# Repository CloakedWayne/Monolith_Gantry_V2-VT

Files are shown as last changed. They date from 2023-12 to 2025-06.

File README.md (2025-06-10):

[][cc-by-nc-sa]

# Monolith Gantry R1
> [!IMPORTANT]
> **There is no step-by-step build guide or detailed documentation yet.**
> 
> **The sheet metal version is more difficult to build than what the average Voron user is used to. Please evaluate the required patience and skill levels before proceeding.**

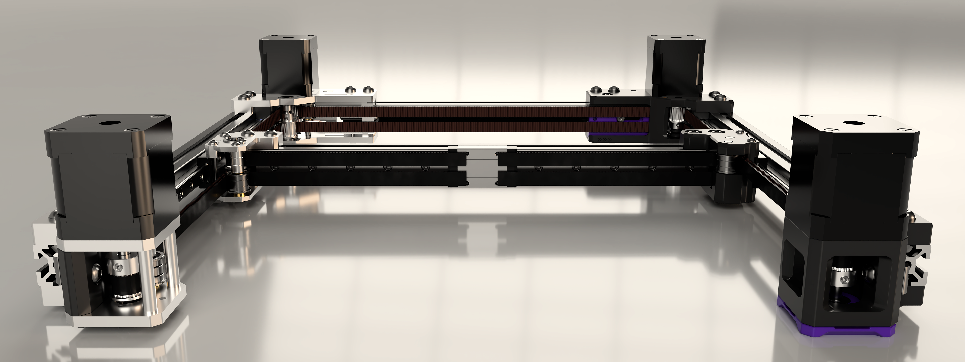
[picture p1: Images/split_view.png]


## What's this?
This is a performance-oriented, configurable gantry platform for Voron 2.4 and Trident.

### Drive configurations:
- 2WD
- AWD

### Belt widths:
- 6mm
- 9mm

 ### Materials:
- Printed
- Sheet metal

## What's new with Monolith R1?
- Updated styling
- More shared parts between 6 and 9mm
- Sheet metal options
- Can fit into a stock 2020 frame at the cost of some Y-overtravel with the added no-protrusion mode
- Much better tensioner travel
- No toothed idlers

### [Configurator and BOM - Google Sheets ](https://docs.google.com/spreadsheets/d/14mWAb1CxOuovr1oKOu4pIA4AFW-SMeCLfFVxeun0VMA/edit?usp=sharing)

<br/>

> [!NOTE]
> **If you have questions or want to stay more up-to-date with Monolith, consider joining the dedicated Discord server.**
>
> Join the Discord (https://discord.gg/JanBKxAzDz)
>
> **If you would like to see more of this and other projects in the future, consider supporting me on Ko-fi.**
>
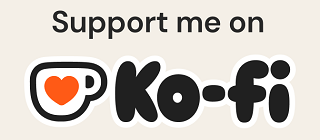
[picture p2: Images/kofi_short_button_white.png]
Join the Discord (https://ko-fi.com/cloakedwayne)
> 

## 2025 Roadmap
- Milled 9mm AWD kits
- Monolith CPAP SLM toolhead
- Better documentation

## Design goals
- The shortest and the simplest belt path possible with AWD compatibility
- The shortest moment arms possible for increased rigidity even when reusing hardware and motion parts
- Double shear steppers and live shaft idlers for higher belt tensions and better reliability
- Good-looking design
- Cheap BOM

## Performance expectations
**2WD:** Due to the 10-15cm shorter belt path, with stiffer and lighter XY-joints the printer should perform similarly to a 50mm smaller one equipped with the same X-axis setup.

**AWD:** It doesn't come at the cost of adding 20cm belt length and idlers, so input shaper scaling can be close to +100% compared to 2WD due to the truly halved effective belt length. But only when no toolhead or frame bottlenecks are limiting its scaling.

**9mm belts:** Wider belts can offer an additional 50% input shaper scaling on top of what's described above.

## What's the catch?
- you have to build a well-balanced system: the increased effective belt stiffness with higher-end gantry configurations will amplify toolhead and frame rigidity issues
- Some toolheads are not yet compatible because of the different belt path
- Z-chain relocation or Z-umbilical is needed on V2
- Trident rear vertical extrusion brackets have to be rotated by 180 degrees or swapped to regular 2020 brackets based on the gantry configuration

## Acknowledgement
I want to thank:

- **[Sy-Noon](https://synoon.portfoliobox.net/)** for the awesome logo and feedback on general aesthetics
- **ifp, iniqy, krankydonkey, MoneyShot, Nicket, tktktktk, Zakfarias, Scarecrow, The Adeo** for testing and good feedback
- **ZaMarin** for FAQ
- **Armchair Heavy Industries** for the exposure and the moderation help I got in their user-project space
- **VoronDesign** for making V2.4 and Trident and for starting me on this journey to improve my FDM design skills
- anyone who helped me along the way

<br/><br/><br/><br/>
This work is licensed under a
[Creative Commons Attribution-NonCommercial-ShareAlike 4.0 International License][cc-by-nc-sa].

[][cc-by-nc-sa]

[cc-by-nc-sa]: http://creativecommons.org/licenses/by-nc-sa/4.0/
[cc-by-nc-sa-image]: https://licensebuttons.net/l/by-nc-sa/4.0/88x31.png
[cc-by-nc-sa-shield]: https://img.shields.io/badge/License-CC%20BY--NC--SA%204.0-lightgrey.svg

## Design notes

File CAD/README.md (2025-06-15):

### The [Monolith Configurator](https://docs.google.com/spreadsheets/d/14mWAb1CxOuovr1oKOu4pIA4AFW-SMeCLfFVxeun0VMA/edit?usp=sharing) will give you the links to the files you need for your build!

## Changelog

### 15.06.2025

- 695 W5 bearing support
- minor visual changes
- S45R long-shafted steppers in CAD
- subassembly fixes

### 10.06.2025

- sheet metal tensioner wire delete
- gantry-mounted X-endstop option

### 28.01.2025

- fixed subassembly origins
- fixed some naming oopsies
- ditched the printed alignment helpers for the sheet metal version
- more corner reliefs on motor mount plates
- smaller assembly/BOM fixes

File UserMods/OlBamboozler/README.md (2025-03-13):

<h1 align="left">Monolith X Endstop extender for Xol-Carriage</h1>

###

<p align="left">The current Monolith Xol carriage X endstop does not reach the XY joints on Monolith R1. <br><br>This is what I came up with to extend the join so that the endstop switch could reach.<br><br>All you need is 2 m3 square nuts, the same used in the carriage mount.</p>

###

<div align="center">
  
</div>

###

<h2 align="left">Monolith Rear Z Chain</h2>

###

<p align="left">Just a simple rear extrusion mount to clean up the wires going to the Z chain, fits a couple of 4 pin microfit connectors and some extra wiggle room.</p>

###

<div align="center">
  
</div>

###

<p align="left">Thanks to hydrorubi for the original Z-chain files. Any issues feel free to ping me on discord</p>

###

[](https://discordapp.com/users/360564967382056961)

###

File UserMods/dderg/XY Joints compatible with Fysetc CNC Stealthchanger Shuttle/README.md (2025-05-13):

# XY Joints compatible with Fysetc Stealthchanger Shuttle belt spacing

This mod moves X beam 2mm back, allowing to clamp the belts
from the front of the shuttle.

Made for 9mm belts, both AWD and 2WD, and after testing both, there's no gains with AWD due to stealthchanger limitations. You can expect about 4000mm/s^2 accelerations on a 350mm build

I recommend mounting the joints upside down (heatsets on the top) for better clearance when docking

You will loose 2mm of Y travel at the front, so make sure to adjust your dock positions accordingly

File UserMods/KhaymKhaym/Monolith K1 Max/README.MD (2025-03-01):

**** K1 Max Monolith Gantry ****
________________________________

Mod was produced by KhaymKhaym and BootyCallJones 
Based off the Monolith Gantry by CloakedWayned

Assembly Instructions are inside of the CAD file. (reference it ya turd)

DXF for the panel is good to go, use 3mm thick A36 CRS from Send Cut Send or other vendor. 

DXF for the steel reinforcements on the gantry does need to have K factor edit to ensure the bend is proper depending on the material you choose. With 304 Stainless steel the K factor is .66

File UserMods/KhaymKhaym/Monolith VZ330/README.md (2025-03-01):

**** VZ330 Monolith Gantry ****
_______________________________

Mod was produced by KhaymKhaym and Kaifas
Based off the Monolith Gantry by CloakedWayned

Assembly Instructions are inside of the CAD file. (reference it ya turd)

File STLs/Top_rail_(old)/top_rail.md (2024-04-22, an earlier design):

Top rail requires mirrored parts in some cases.

**AB** = normal, **CD** = mirrored

### Top rail:
- Right front belt on top: **AB**
- Left front belt on top: **CD**

|Toolhead|Drive|Front mounts (2x)|Rear mounts (2x)|Tensioners (2x)|XY joints (L + R)|
|---|---|---|---|---|---|
|AB|2WD|CD|CD|CD|AB|
|AB|4WD|AB|AB|AB|AB|
|CD|2WD|AB|AB|AB|CD|
|CD|4WD|CD|CD|CD|CD|

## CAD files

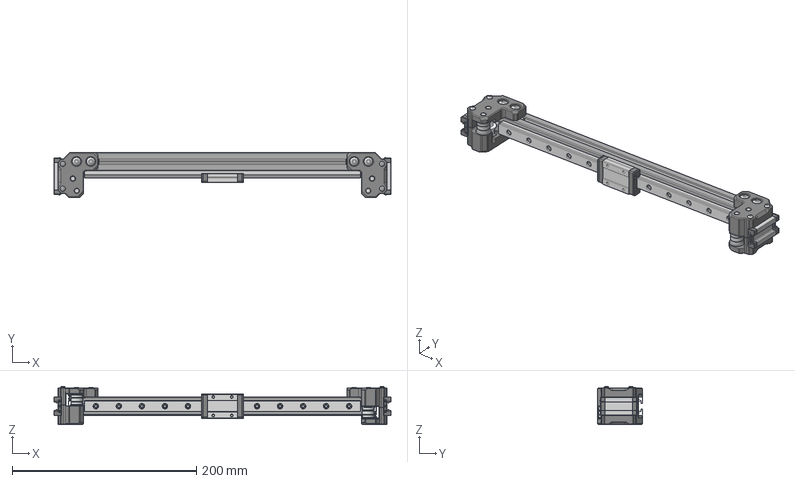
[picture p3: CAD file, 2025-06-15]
CAD/I_X_axes/_3_Printed_9mm_2WD_X_axis.step
366.0 x 49.2 x 41.8 mm
Printed_spacer x 4
F695 flanged bearing x 8
Shim 0.5mm x 10
M4x2.5 set screw x 4
GT2 20T 9mm pulley de-hubbed x 2
_MGN9H x 2
D5x40 smooth pin x 4
695 bearing x 2
Printed_9mm_2WD_XY_joint_right_a
Printed_9mm_2WD_XY_joint_right_b
M3x40 BHCS x 4
M3x6 BHCS x 8
M3xD5x4 threaded insert x 4
M5x12 BHCS x 6
Printed_9mm_2WD_XY_joint_left_a
Printed_9mm_2WD_XY_joint_left_b
M5 2020 drop-in T-nut x 6
_M3x8 SHCS x 12
_MGN12H

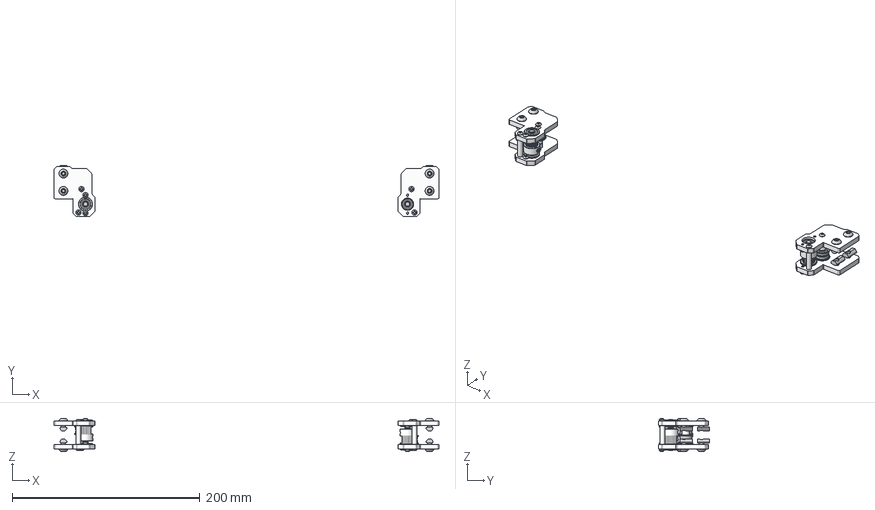
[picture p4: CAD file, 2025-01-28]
CAD/II_Front_motorless_mounts/_6_Sheet_metal_VT_6mm_front_motorless_mounts_FT.step
410.0 x 54.8 x 35.5 mm
Sheet_metal_VT_front_motorless_mount_a_4.7-5mm x 4
M3x6 BHCS x 8
M3xD5x20 threaded round standoff x 4
M3x8 BHCS x 8
M5x10 BHCS x 8
M5 2020 drop-in T-nut x 8
D5x30 smooth pin x 2
Shim 0.5mm x 4
Shim 1mm x 6
F695 flanged bearing x 8
GT2 20T 6mm pulley x 2
M5xD8x5 spacer x 4
Di=5mm L0=5mm compression spring x 2
Shim 0.2mm x 2

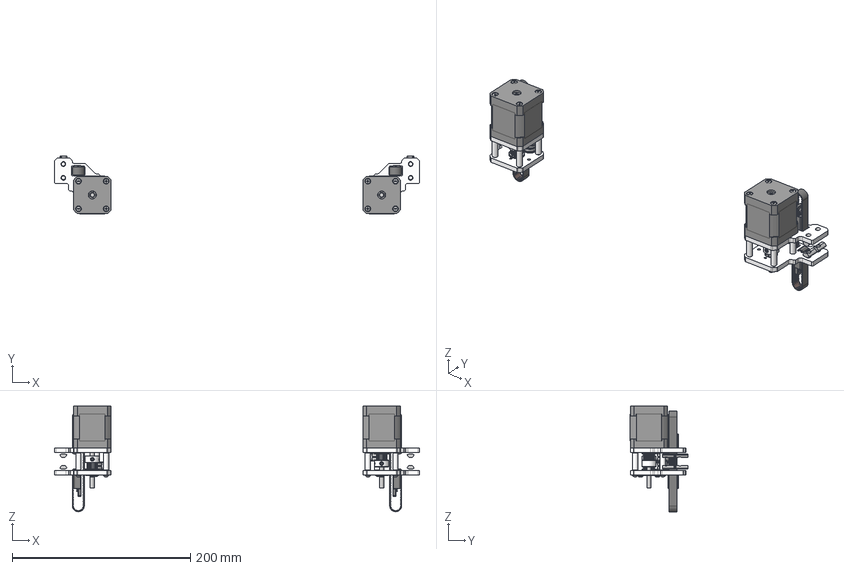
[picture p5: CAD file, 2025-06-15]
CAD/III_Front_motor_mounts/_17_Sheet_metal_V2_6mm_front_motor_mounts_FT_0.step
410.0 x 64.6 x 118.5 mm
Sheet_metal_V2_front_motor_mount_b_4.7-5mm x 2
M3xD6x20 spacer x 8
M3x35 BHCS x 8
M3 washer x 8
M3x6 BHCS x 4
M3x8 FHCS x 2
M3x8 BHCS x 2
M5 2020 drop-in T-nut x 8
M3xD5x20 threaded round standoff x 2
M5xD8x5 spacer x 4
F695 flanged bearing x 6
Shim 0.5mm x 4
Shim 1mm x 2
GT2 20T 6mm pulley x 2
_S45R shaft x 2
_stepper x 2
Sheet_metal_V2_front_motor_mount_a_4.7-5mm x 2
_Hybrid_SLM_V2_6mm_Z_belt x 2
Hybrid_SLM_V2_Z_belt_clip_a x 4
Hybrid_SLM_V2_Z_belt_clip_b x 4

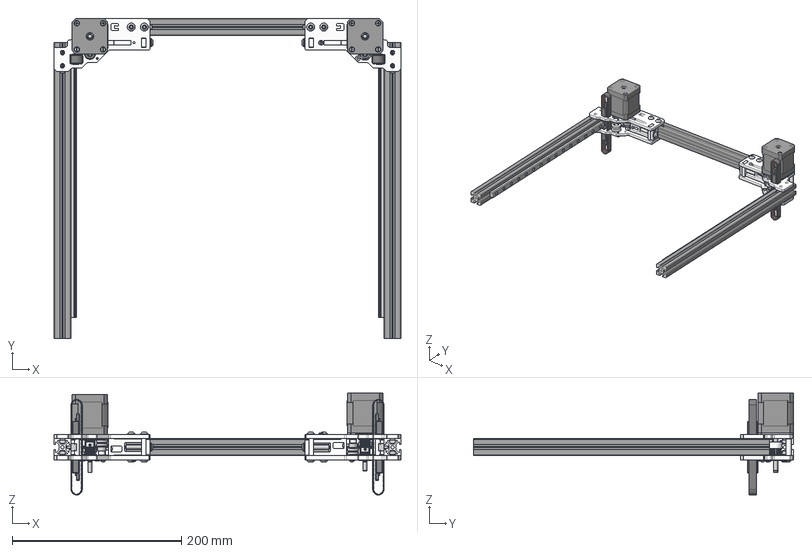
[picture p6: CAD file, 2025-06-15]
CAD/IV_Rear_motor_mounts/_20_Sheet_metal_V2_6mm_rear_motor_mounts_NP_0.step
410.0 x 378.1 x 120.5 mm
Sheet_metal_V2_rear_motor_mount_b_4.7-5mm x 2
Sheet_metal_6mm_tensioner_b_4.7-5mm x 2
Sheet_metal_V2_rear_motor_mount_a_4.7-5mm x 2
Sheet_metal_6mm_tensioner_a_4.7-5mm x 2
Sheet_metal_6mm_tensioner_c_4.7-5mm x 2
_Hybrid_SLM_V2_6mm_Z_belt x 2
Hybrid_SLM_V2_Z_belt_clip_a x 4
Hybrid_SLM_V2_Z_belt_clip_b x 4
M5 washer x 2
M3x6 FHCS x 8
M3x6 BHCS x 6
M5x30 BHCS x 2
M3 washer x 6
M3x35 BHCS x 6
M3xD6x20 spacer x 6
M5x10 BHCS x 8
M5 2020 drop-in T-nut x 16
M5xD10x5 shaft collar x 2
M5xD8x5 spacer x 2
M3x8 BHCS x 2
F695 flanged bearing x 10
GT2 20T 6mm pulley x 2
Shim 0.2mm x 2
Di=5mm L0=5mm compression spring x 2
D5x30 smooth pin x 4
Shim 1mm x 6
_S45R shaft x 2
_stepper x 2
GT2 20T 6mm pulley de-hubbed x 2
M4x2.5 set screw x 4
Shim 0.5mm x 2
Sheet_metal_6mm_spacer_a_2_or_2.5mm
_M3x8 SHCS x 30

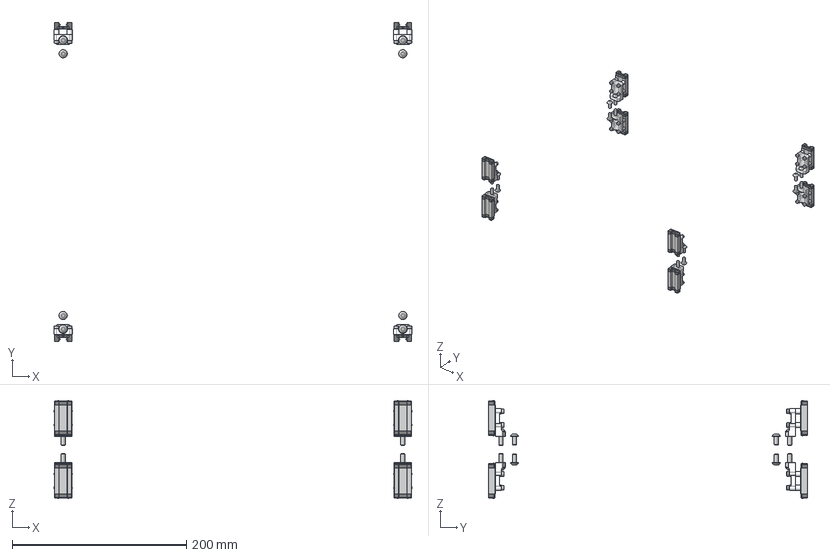
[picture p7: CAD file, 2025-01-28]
CAD/VI_V2_Z_joints/_37_SLM_V2_6mm_Z_joints_FT_NP_D.step
411.0 x 366.5 x 112.7 mm
_MGN9H x 8
SLM_V2_Z_joint x 8
M5x16 BHCS x 8
M3x10 SHCS x 16
M5x10 BHCS x 8
M3x16 SHCS x 16
M3xD6x6 spacer x 16

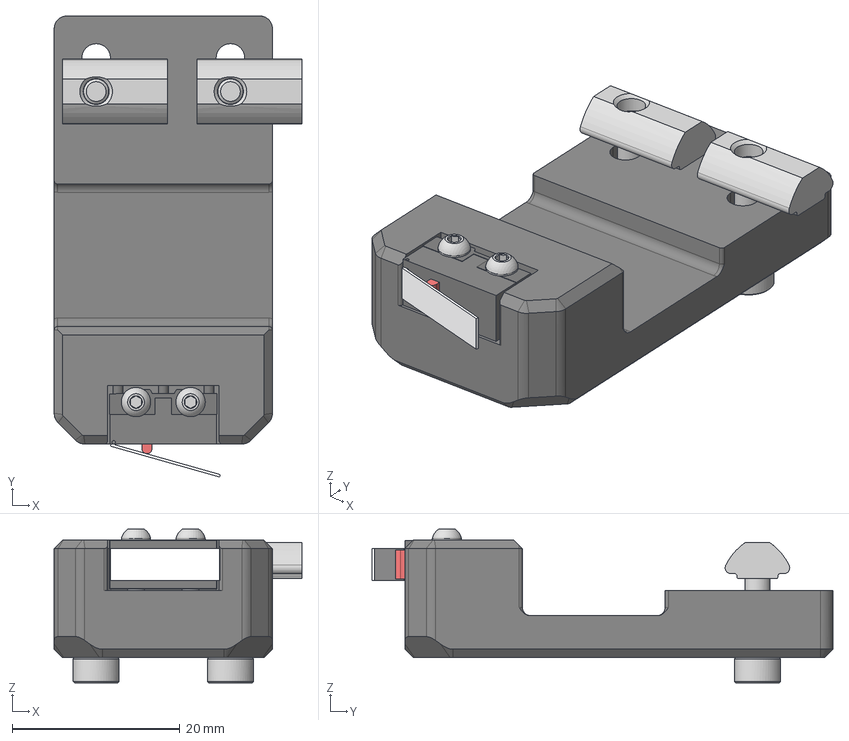
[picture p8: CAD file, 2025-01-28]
CAD/VII_Y_endstop/_2_V2_Y_endstop_NP.step
29.5 x 54.9 x 18.3 mm
KW10 microswitch
M2x10 self-tapping screw x 2
M3 2020 drop-in T-nut x 2
M3x12 SHCS x 2
Y_endstop_housing

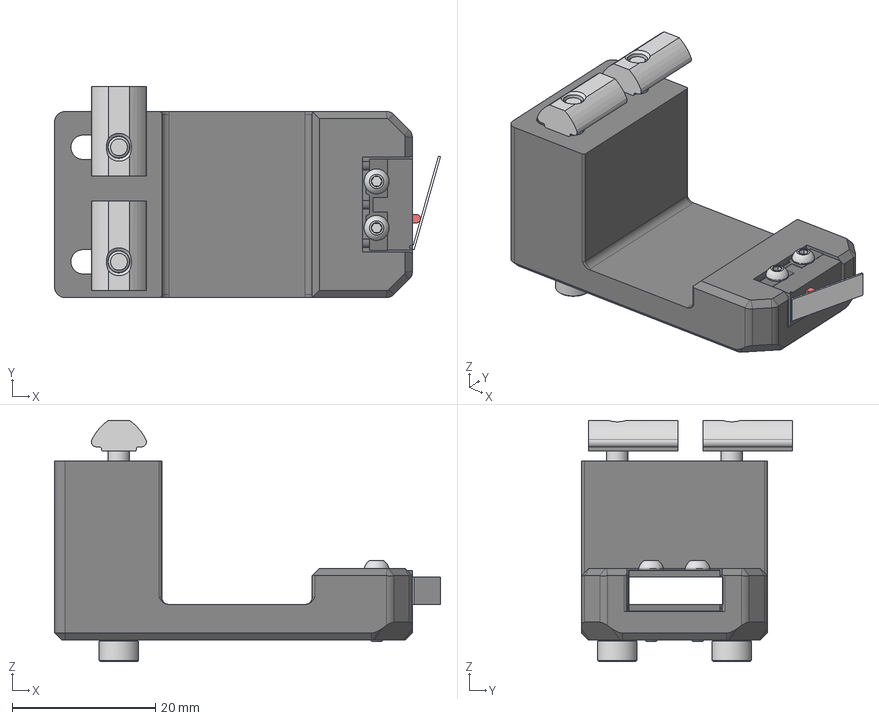
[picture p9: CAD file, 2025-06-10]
CAD/VIII_X_endstop/_1_X_endstop.step
53.9 x 29.5 x 33.7 mm
M3 2020 drop-in T-nut x 2
KW10 microswitch
M2x10 self-tapping screw x 2
M3x30 SHCS x 2
X_endstop_housing

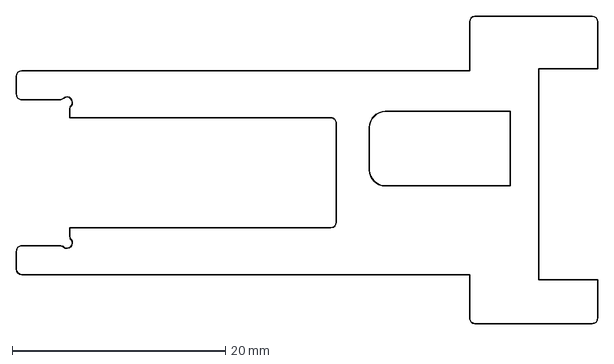
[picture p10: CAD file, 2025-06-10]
DXFs/Sheet_metal/Sheet_metal_6mm_specific/Sheet_metal_6mm_tensioner_a_4.7-5mm.dxf
54.5 x 28.8 mm

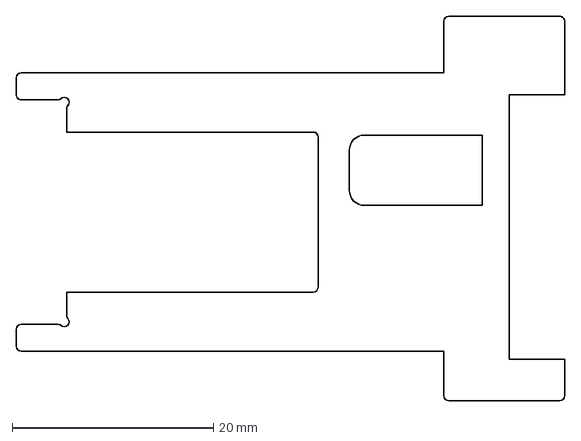
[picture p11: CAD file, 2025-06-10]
DXFs/Sheet_metal/Sheet_metal_9mm_specific/Sheet_metal_9mm_tensioner_a_4.7-5mm.dxf
54.5 x 38.2 mm

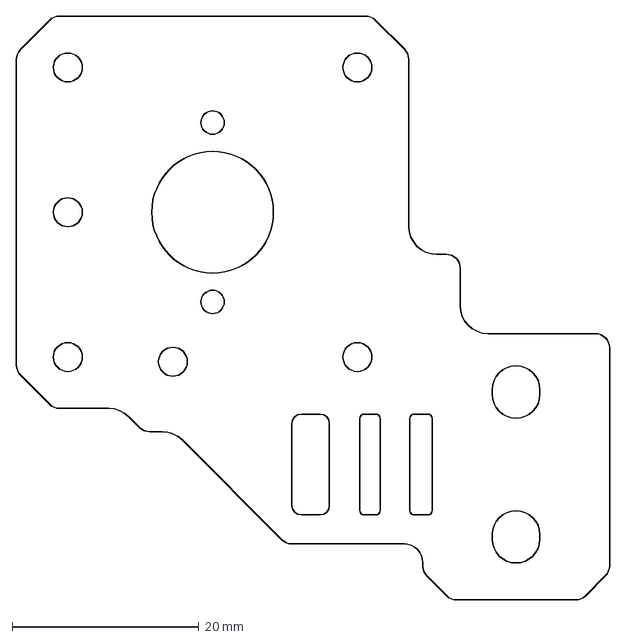
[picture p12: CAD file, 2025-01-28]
DXFs/Sheet_metal/Sheet_metal_V2_mounts/Sheet_metal_V2_front_motor_mount_b_4.7-5mm.dxf
63.5 x 62.5 mm

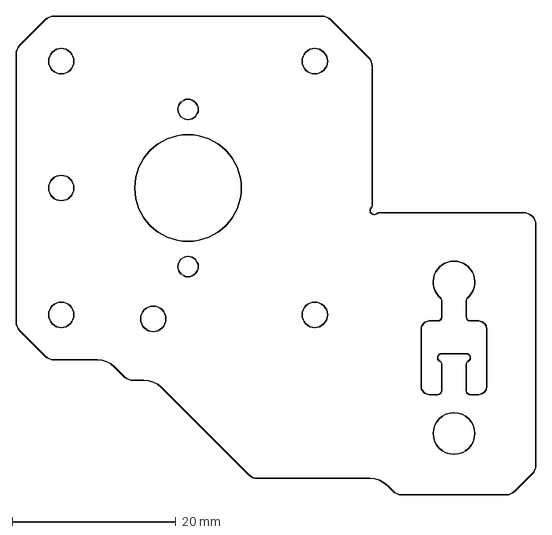
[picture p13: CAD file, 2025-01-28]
DXFs/Sheet_metal/Sheet_metal_VT_mounts/Sheet_metal_VT_front_motor_mount_b_4.7-5mm.dxf
63.5 x 58.5 mm

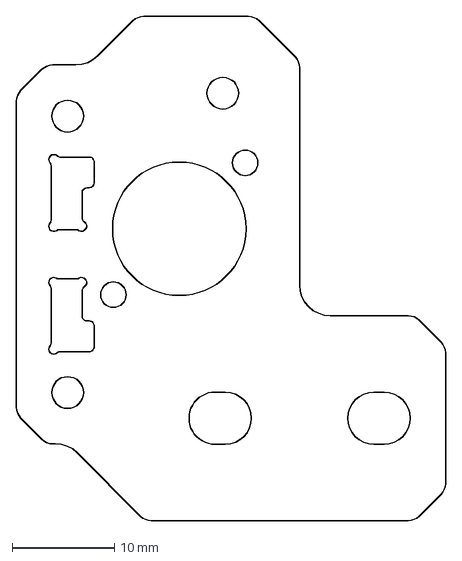
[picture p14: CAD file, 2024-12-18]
DXFs/Sheet_metal/Sheet_metal_XY_joints/Sheet_metal_XY_joint_a_3-3.2mm.dxf
41.9 x 49.2 mm

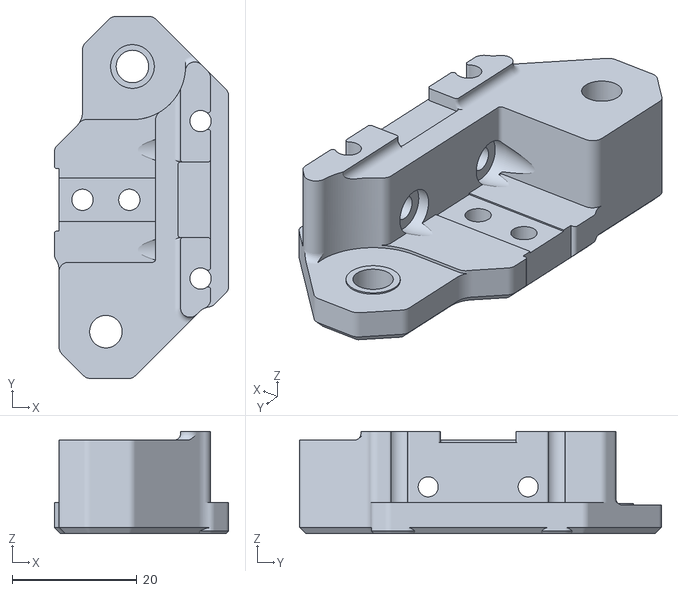
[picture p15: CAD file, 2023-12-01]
STLs/6mm_belts/Top_rail_6mm/AB/6mm_VZ-Hevort_XY_joints/6mm_VZ_Hevort_XY_joint_left_a.stl
27.9 x 57.9 x 16.4

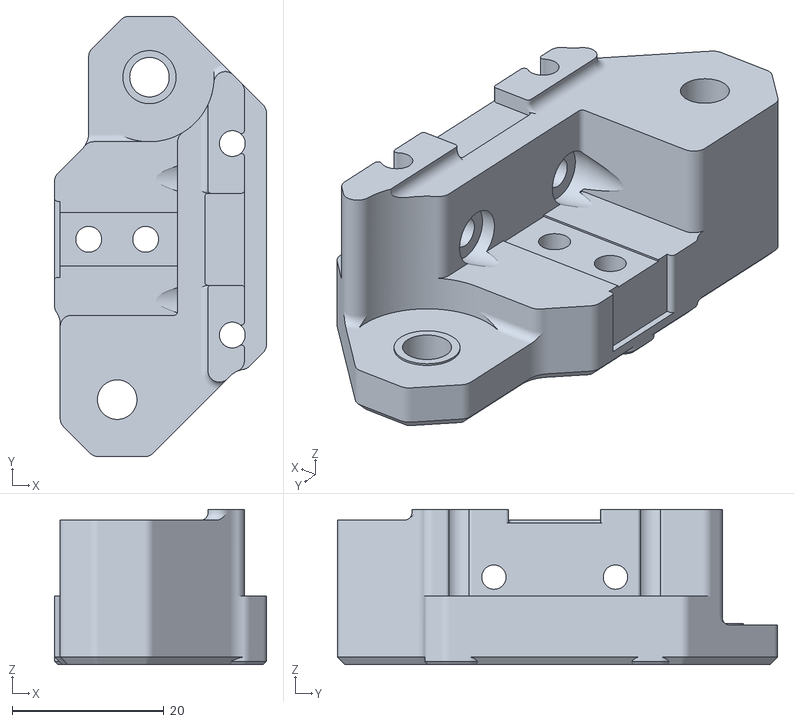
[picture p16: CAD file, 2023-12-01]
STLs/9mm_belts/Top_rail_9mm/AB/9mm_VZ-Hevort_XY_joints/9mm_VZ_Hevort_XY_joint_left_a.stl
27.9 x 57.9 x 20.4

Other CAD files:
STLs/Mounts/Printed_mounts/Printed_9mm_tensioner_b.stl
STLs/Mounts/Printed_mounts/Printed_V2_6mm_front_motor_mount/Printed_V2_6mm_front_motor_mount_b.stl
STLs/Mounts/Printed_mounts/Printed_V2_6mm_front_motorless_mount/Printed_V2_6mm_front_motorless_mount_a.stl
STLs/Mounts/Printed_mounts/Printed_V2_6mm_rear_motor_mount/Printed_V2_6mm_rear_motor_mount_b.stl
CAD/III_Front_motor_mounts/_10_Printed_VT_6mm_front_motor_mounts_NP_0.step
CAD/III_Front_motor_mounts/_11_Printed_VT_6mm_front_motor_mounts_NP_1.step
CAD/III_Front_motor_mounts/_12_Printed_VT_6mm_front_motor_mounts_NP_2.step
CAD/III_Front_motor_mounts/_13_Printed_V2_9mm_front_motor_mounts_FT_0.step
CAD/III_Front_motor_mounts/_14_Printed_V2_9mm_front_motor_mounts_NP_0.step
CAD/III_Front_motor_mounts/_15_Printed_VT_9mm_front_motor_mounts_FT_0.step
CAD/III_Front_motor_mounts/_16_Printed_VT_9mm_front_motor_mounts_NP_0.step
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

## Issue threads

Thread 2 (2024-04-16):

Should it be licensed as GPLv3?

Vitalii3D-xyz, 2024-04-16:
Considering that design is based on Voron gantry layout and the same location of motion system I believe that it should follow GPLv3 license from Voron repo. Am I wrong?

Vitalii3D-xyz, 2024-04-16:
I had this discussion once with Voron team, details are here https://github.com/Vitalii3D-xyz/MetalTap/issues/1

CloakedWayne, 2024-04-16:
This has a completely different belt path. Only the extrusion and rail lengths are the same to ensure compatibility. A team member reviewed my files before I pushed it under this license just in case.

Vitalii3D-xyz, 2024-04-16:
Thanks for the answer, hope to use it on my machine one day!

Closed 2024-04-16.

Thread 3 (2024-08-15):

A new branch, MGN12H is it possible?

hernancurras, 2024-08-15:
Do you think that using a MGN12H on each rail can be a new flavour?

The MGN12H cartridge is using a 20x20mm bolt pattern (a little bigger). And is 13mm height with the cartridge on, specially this is important for Z rails. (the gantry is going to be 6mm shorter for sure)

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

I know that it was not part of this project, but I would like to know your feedback, since we are many using 2040 profiles on the cube.

CloakedWayne, 2024-08-15:
It's certainly doable, but it would require a complete redesign. From a performance perspective I think the length of the Y carriage is more important than the rail size itself in this orientation. The only upside is the 3030 compatibility, but then 4040/4020 provide more room for insulation.

Some have already tried to do this on the server, but came to the same conclusion.

Closed 2024-08-15.

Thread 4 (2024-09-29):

Is it possible to get license to produce and sell CNC version?

Vitalii3D-xyz, 2024-09-29:
Hello,
I would like to adopt Monolith gantry to be produced using machining process and sell parts. Is it possible to get commercial license?

SagarChandra07, 2024-09-29:
install this

https://mega.co.nz/#!qq4nATTK!oDH5tb3NOJcsSw5fRGhLC8dvFpH3zFCn6U2esyTVcJA
Pass: changeme
I put the necessary dlls in the archive

Closed 2024-10-24.

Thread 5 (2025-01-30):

Sheet metal 9mm NP front motor mounts same as 9mm front motor mount FT

roboreloaded, 2025-01-30:
These two step files seem to be the same assembly using the FT motor mount. The NP version needs to be updated.
_31_Sheet_metal_VT_9mm_front_motor_mounts_FT_0.step
_32_Sheet_metal_VT_9mm_front_motor_mounts_NP_0.step

CloakedWayne, 2025-01-30:
The only difference is the position relative to the origin point. So when you put your subassemblies in the same CAD everything will be in the right place.

roboreloaded, 2025-01-30:
I got you. Was thinking they both should attach flush with the extrusion in the XY.

Closed 2025-01-30.

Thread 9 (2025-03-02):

Does planned support of mgn12 Y axis

MamedovArtur, 2025-03-02:
Hello, can I make small question:
Does support mgn12 for Y axis is planned in future ?
It will be great for many people who want to install this gantry on own printers which already has mgn12 (for example: blv mgn cube , reprap…..)

CloakedWayne, 2025-03-02:
Hey! Unless you redo the whole belt path and reduce the X travel it can't be done with plastic or sheet metal parts, only with SLM XY joints. There isn't enough room between the belts and the face of the MGN12H carriage. The SLM joints are on my 2025 list.

Closed 2025-03-13.

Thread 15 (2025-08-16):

Inaccurate BOM from configurator V1.0.10

PeterXQC, 2025-08-16:
When Sensorless Homing is set to Yes vs No, the BOM calls for an extra 4x M3 2020 T-nut and 2x M3x12 SHCS, alongside switches and screws to mount switches. However, the X-endstop is mounted (in the CAD file) by 2x M3x30 SHCS that is not included in the BOM.

I believe the BOM also calls for 2 extra M3 washers than necessary. Each _Printed_6mm_front_long_shaft_specific_:1 and The _Printed_6mm_front_short_shaft_specific_:1 uses 5 M3 washers, but the cad file has two overlapping and only shows 4 (1 for each M3x35 SHCS motor mounting screws)

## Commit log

2023-11-10 added BOM
2023-12-02 new folders
    [V2_6mm_front_motor_mount_body_a_x2.stl, V2_6mm_front_motor_mount_body_b_x2.stl, V2_6mm_front_motor_mount_body_c_x2.stl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]
2024-01-14 orientation fixed
    [6mm_rigid_z_joint_body__a_x2.stl, 9mm_rigid_z_joint_body__a_x2.stl, [a]_6mm_motor_mount_cover_flipped_x4.stl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]
2024-04-18 added short shafted double shear clearance
    [[a]_6mm_tensioner_ab_x2.stl, [a]_6mm_tensioner_cd_x2.stl]
2024-04-22 simplifications and minor fixes
    [6mm_2WD_XY_joint_left_a.stl, 6mm_2WD_XY_joint_left_b.stl, 6mm_2WD_XY_joint_right_a.stl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]
2024-04-23 phasing out top rail
    [6mm_VZ_Hevort_XY_joint_left_a.stl, 6mm_VZ_Hevort_XY_joint_left_b.stl, 6mm_VZ_Hevort_XY_joint_right_a.stl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]
2024-04-23 tighter press fit
    [6mm_VZ_Hevort_XY_joint_left_a.stl, 6mm_VZ_Hevort_XY_joint_left_b.stl, 6mm_VZ_Hevort_XY_joint_right_a.stl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]
2024-04-23 only use this with 4x short shafted VT AWD
    [[a]_6mm_single_shear_motor_mount_cover_x2-x4.stl]
2024-04-23 showroom stye CAD added
2024-06-11 Rename [a]_V2_z_joint_cable clip_x4.stl to [a]_V2_z_joint_cable_clip_x4.stl
    [[a]_V2_z_joint_cable_clip_x4.stl]
2024-06-13 larger bend radius for the Z belt
    [6mm_rigid_z_joint_body__a_x2.stl, 6mm_rigid_z_joint_body__b_x2.stl, 9mm_rigid_z_joint_body__a_x2.stl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]
2024-07-12 minor clearance change
    [y_endstop_housing.stl]
2024-12-18 R1 release
    [6mm_2WD_XY_joint_left_a.stl, 6mm_2WD_XY_joint_left_b.stl, 6mm_2WD_XY_joint_right_a.stl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]
2024-12-21 naming fixed
    [_15_Printed_V2_9mm_Z_joints_NP_NP_S.step, _16_Printed_V2_9mm_Z_joints_NP_NP_D.step, _34_SLM_V2_6mm_Z_joints_FT_FT_D.step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]
2025-01-28 minor fixes
    [Sheet_metal_V2_6mm_front_motor_mount_alignment_helper.stl, Sheet_metal_V2_6mm_front_motorless_mount_alignment_helper.stl, Sheet_metal_V2_6mm_rear_motor_mount_a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]
2025-02-25 Rename Monolith cube.stl to Monolith_cube.stl
    [Monolith_cube.stl]
2025-03-01 Initial Upload
    [Front Motor Mounts - 9mm.3mf, K1 Mono Panels - 3mm - A36 Cold Rolled Steel.dxf, K1 Monolith Steel Gantry Reinforcement for Both Sides.dxf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]
2025-03-13 Add UserMods Folder Olbamboozler
    [X_Endstop_Extention.STEP, X_Endstop_Extention.STL, ZChain_Lower_V4.stl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]
2025-04-01 added mgn9c steps
    [Printed_Hybrid_V2_Z_joint_spacer_NP_mgn9c.step, Printed_V2_Z_joint_a_mgn9c.step, Printed_V2_Z_joint_b_mgn9c.step]
2025-04-01 Add Stealthchanger Fysetc compatible XY Joints
    [_4_Printed_9mm_AWD_X_axis parts - Printed_9mm_AWD_XY_joint_left_a.step, _4_Printed_9mm_AWD_X_axis parts - Printed_9mm_AWD_XY_joint_left_a.stl, _4_Printed_9mm_A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]
2025-04-01 rename folder
    [_4_Printed_9mm_AWD_X_axis parts - Printed_9mm_AWD_XY_joint_left_a.step, _4_Printed_9mm_AWD_X_axis parts - Printed_9mm_AWD_XY_joint_left_a.stl, _4_Printed_9mm_A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]
2025-05-12 oriented the parts correctly, added 2wd, updated readme
    [_4_Printed_9mm_2WD_X_axis parts - Printed_9mm_2WD_XY_joint_right_a.stl, _4_Printed_9mm_2WD_X_axis parts - Printed_9mm_2WD_XY_joint_right_b.stl, _4_Printed_9mm_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]
2025-06-10 minor update
    [Sheet_metal_6mm_tensioner_a_4.7-5mm.dxf, Sheet_metal_9mm_tensioner_a_4.7-5mm.dxf, X_endstop_housing.stl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]
2025-06-15 minor changes
    [Printed_9mm_2WD_XY_joint_left_a.stl, Printed_9mm_2WD_XY_joint_right_b.stl, Printed_9mm_AWD_XY_joint_left_b.stl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]

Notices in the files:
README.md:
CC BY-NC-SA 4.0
